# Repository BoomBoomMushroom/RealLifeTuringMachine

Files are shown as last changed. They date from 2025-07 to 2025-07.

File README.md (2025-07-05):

# Real Life Turing Machine
This is a real, physical, and working Turing Machine using an ESP32, off the shelf i2c components, and NFC tags. The Turing machine seems like the lowest level and most basic form of hardware imaginable, so I wanted to try my hand at making one in real life!

# Images
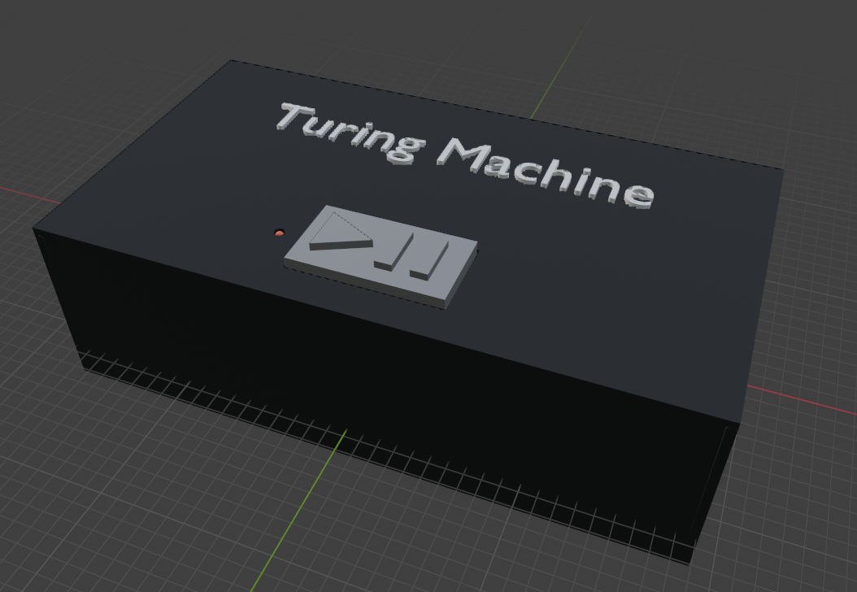
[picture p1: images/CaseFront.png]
Case Front

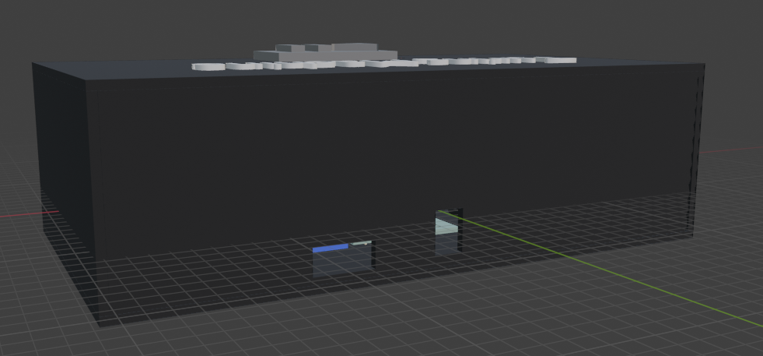
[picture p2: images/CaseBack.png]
Case Back

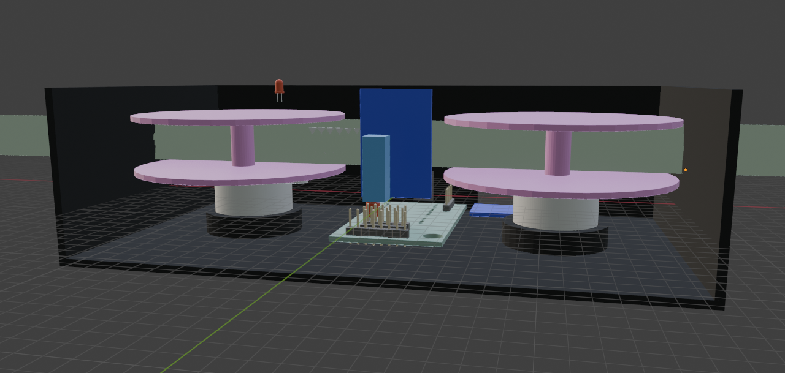
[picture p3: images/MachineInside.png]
Machine Inside

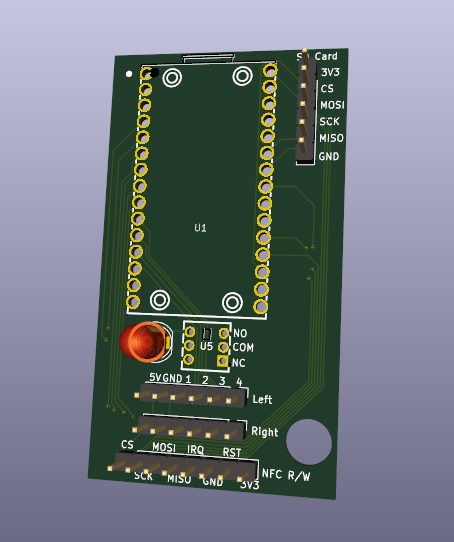
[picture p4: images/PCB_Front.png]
PCB


# Hackatime project name(s)
- RealLifeTuringMachine (8h 31m) TODO: Update this time before submitting
- PCB (2h 23m)
- ESP32_OnlineDevBoard (19m)
- SD_Card_Amazon (10m)
- VHS_Container (4m)
- Blender-VHS_Container (2m)
- Blender-TuringMachineCAD_Models (2m)

# BOM (Check BOM.md for a more in depth bill of materials)
- NFC Stickers
- NFC Reader & Writer Module
- 2x 28BYJ-48 Stepper Motors & Driver boards
- 50ft to 100ft Mylar/Polyester 16mm Film Leader
- ESP32
- SD Card Breakout Board + SD Card (optional)
- Latching Switch 6 Pin
- 3D Printer filament if 3d printing the case
- 3mm LED
- PCB to house all the electronics

TODO: Fill out the checklist and submit

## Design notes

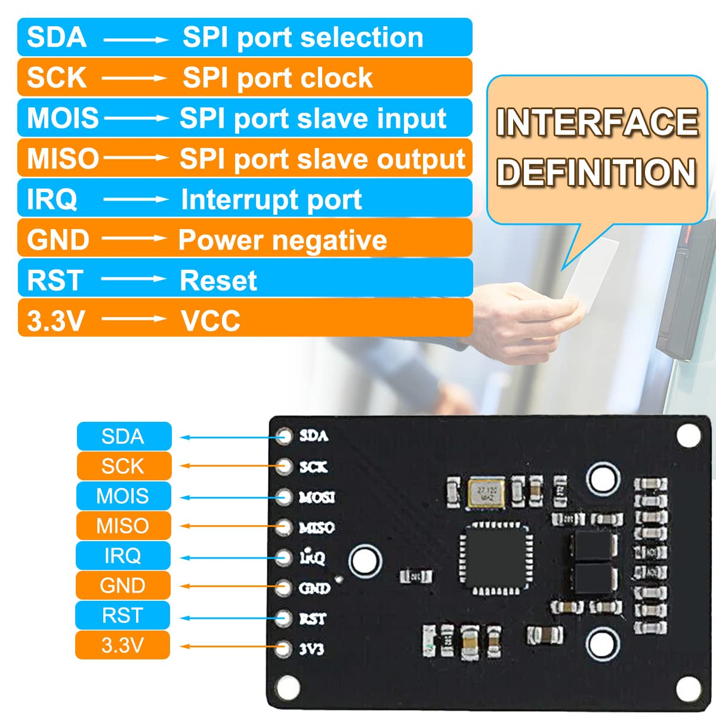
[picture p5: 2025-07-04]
NFC_Reader_Pinout.png

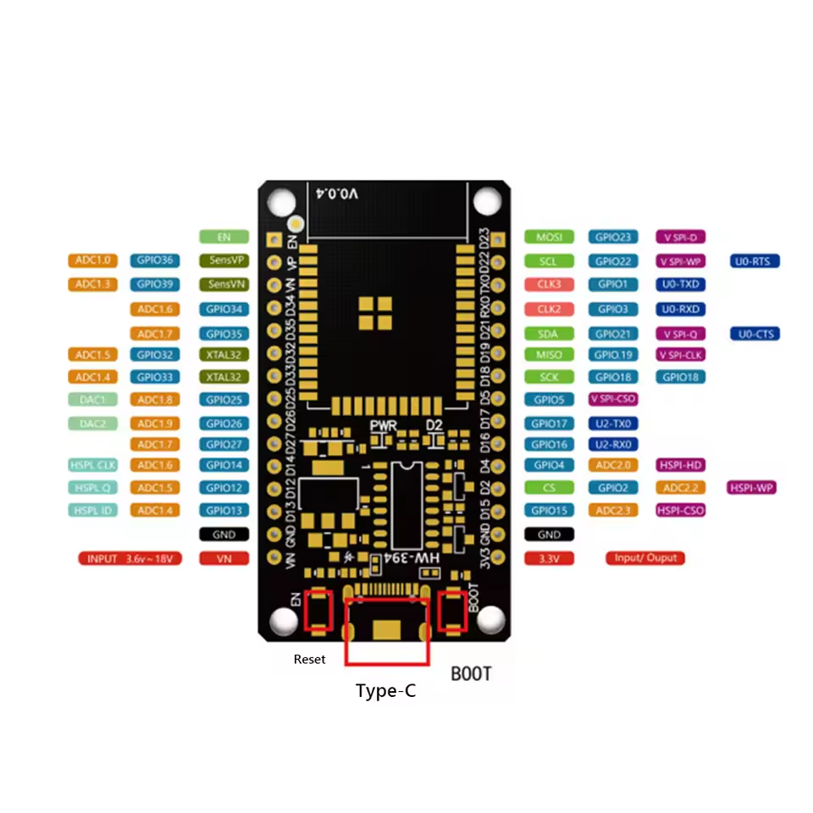
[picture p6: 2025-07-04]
ESP32_Pinout.png

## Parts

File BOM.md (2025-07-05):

# NFC (total: 8.40)
    NFC Stickers: $7.39 100pcs https://www.aliexpress.us/item/3256807427594021.html
    NFC Reader + Writer (i2c?): $1.81 https://www.aliexpress.us/item/2251832854399567.html

# Tape Parts (total: 21.12)
    Stepper Motors + Driver Board: $5.12 total, $2.56 per 28BYJ-48, https://www.aliexpress.us/item/3256806163054731.html
    Tape Material: $16, $8 leader + $8 shipping Mylar/Polyester 16mm Film Leader Cream Single Perf, https://hollywoodfilmsupplies.com/film-supplies/16mm-film-leader-plastic-kodak

# Other Parts (total: 4.67)
    Micro Controller: Aliexpress $1.41 for 2; ESP32, with USB C on it, https://www.waveshare.com/nodemcu-32s.htm  https://www.aliexpress.us/item/3256806150650156.html
    SD Card slot: $1.26 https://www.aliexpress.us/item/3256806636964149.html
    Latching Switch for enable and disabling: $2 https://www.aliexpress.us/item/3256807666498267.html
        Datasheet & Footprints for switch: https://lcsc.com/product-detail/image/KFC7070-Z_C22459508.html

# 3D Printer (optional) (total: 14.99)
    3D Printer Filament PLA: $14.99 https://www.microcenter.com/product/611533/inland-285mm-black-pla-3d-printer-filament-1kg-spool-(22-lbs)

# PCB (total: 5.12)
    PCB from JLCPCB (w/ Global Standard Direct Line Shipping): $5.12

# Grand Total (excluding filament and shipping): $39.31

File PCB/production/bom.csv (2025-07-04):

Designator | Footprint | Quantity | Value | LCSC Part #
D1 | LED_D5.0mm | 1 | EnabledLED
J1 | PinHeader_1x08_P2.54mm_Vertical | 1 | NFC/RFID RW
U1 | ESP32_OnlineDevBoard | 1 | ~
U2, U3, U4 | PinHeader_1x06_P2.54mm_Vertical | 3 | ~
U5 | SW-TH_6P-L7.0-W7.0-P2.00_KFC7070-Z | 1 | ~

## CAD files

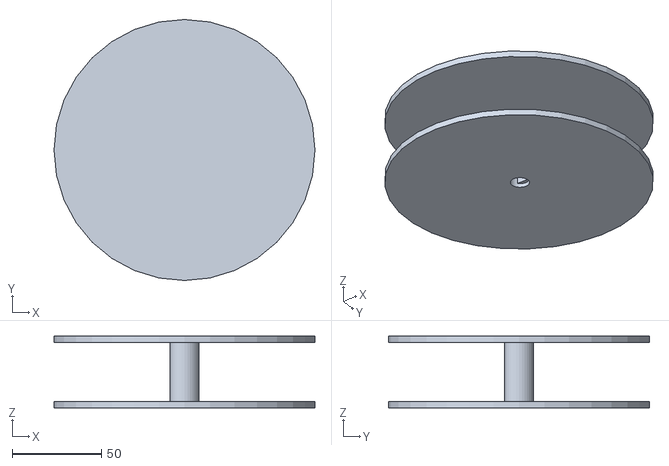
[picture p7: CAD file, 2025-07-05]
CAD_STL/MotorFilmSpool.stl
146.0 x 146.0 x 40.0

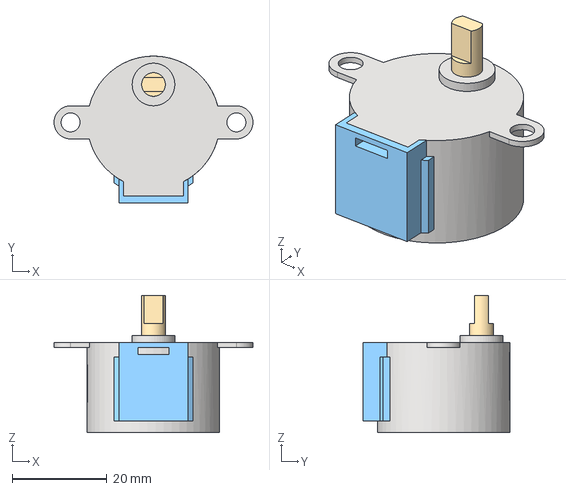
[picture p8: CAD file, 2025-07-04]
TuringMachineCAD_Models/28BYJ-48.step
42.0 x 31.0 x 29.0 mm

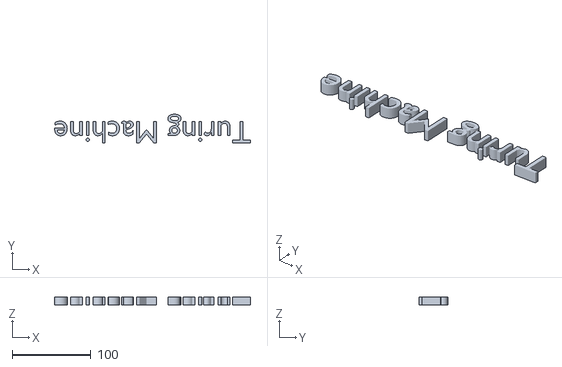
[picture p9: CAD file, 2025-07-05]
CAD_STL/TuringCaseText.stl
248.7 x 36.5 x 10.0

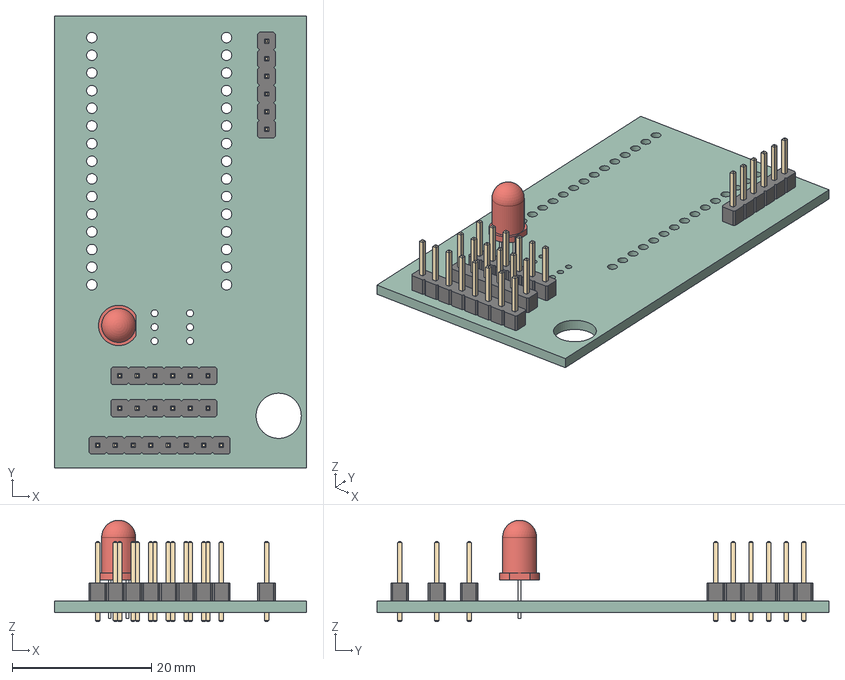
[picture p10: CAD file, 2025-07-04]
TuringMachineCAD_Models/PCB.step
36.2 x 65.0 x 14.6 mm
PinHeader_1x06_P254mm_Vertical x 3
LED_D5.0mm
PinHeader_1x08_P254mm_Vertical
PCB_PCB

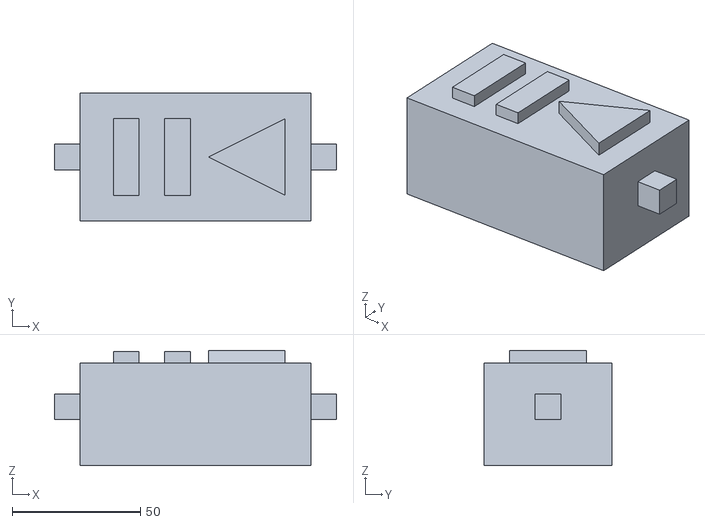
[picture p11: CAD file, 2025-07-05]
CAD_STL/PlayButton.stl
110.0 x 50.0 x 45.0

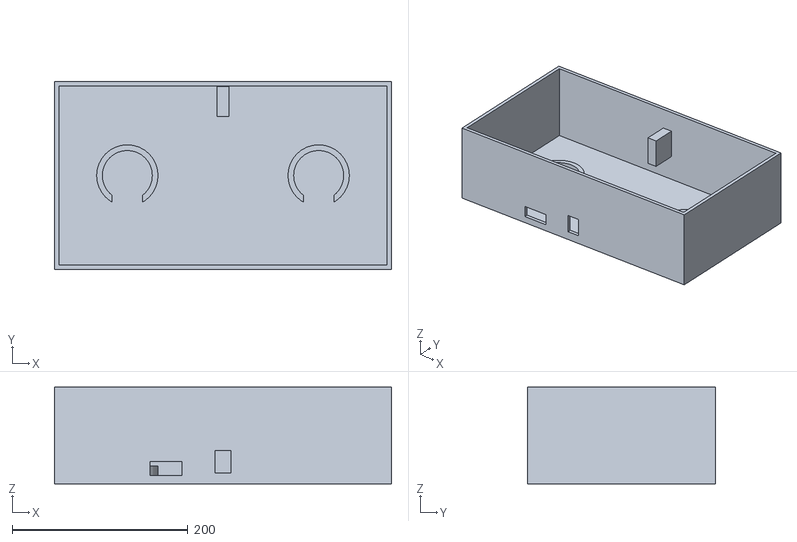
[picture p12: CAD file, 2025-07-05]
CAD_STL/CaseBottomAndWalls.stl
384.0 x 214.0 x 110.0

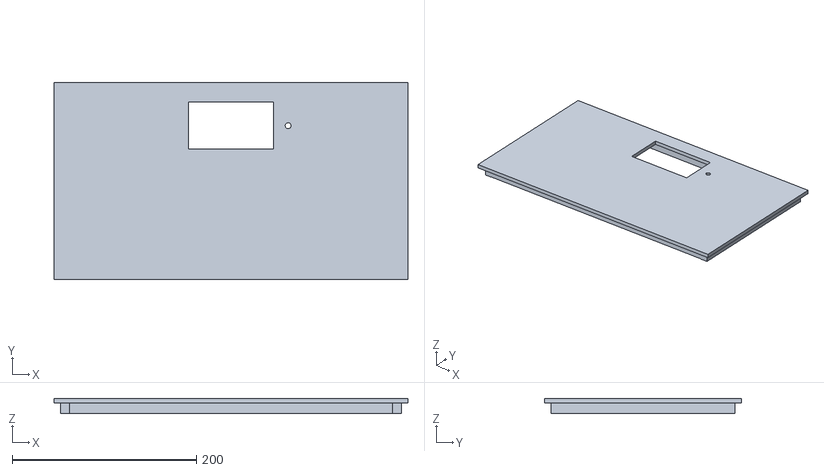
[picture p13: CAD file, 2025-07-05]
CAD_STL/CaseTop.stl
384.0 x 214.0 x 16.5

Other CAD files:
TuringMachineCAD_Models/VHS_Container.blend

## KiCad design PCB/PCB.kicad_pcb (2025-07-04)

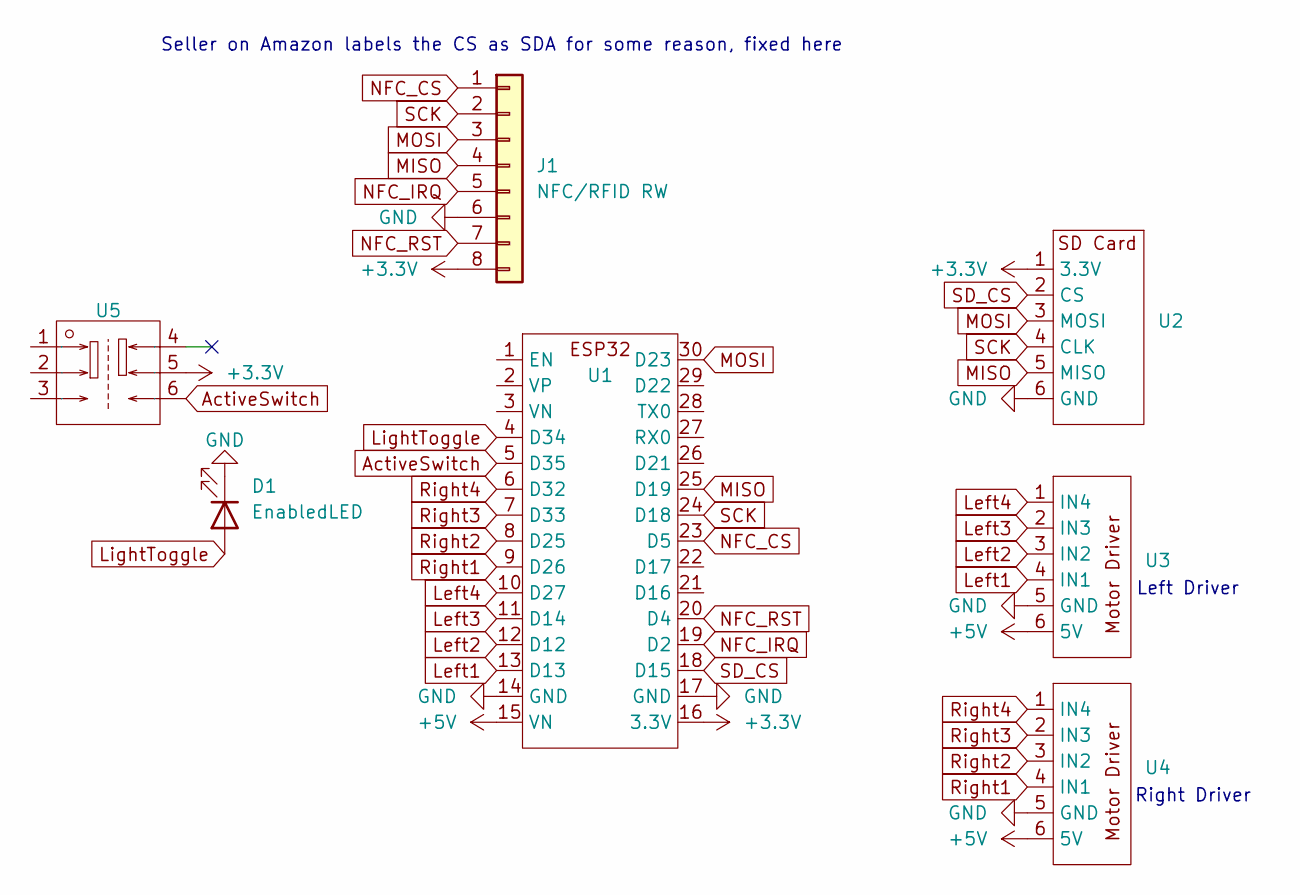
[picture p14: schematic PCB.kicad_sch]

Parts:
D1: EnabledLED; LED_D5.0mm
J1: NFC/RFID RW; PinHeader_1x08_P2.54mm_Vertical
U1: ESP32_OnlineDevBoard
U2, U3, U4: PinHeader_1x06_P2.54mm_Vertical
U5: SW-TH_6P-L7.0-W7.0-P2.00_KFC7070-Z; Manufacturer Part KFC7070-Z; LCSC Part Name KFC7070-Z

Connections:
+3.3V: J1.8, U1.16 (3.3V), U2.1 (3.3V), U5.5
+5V: U1.15 (VN), U3.6 (5V), U4.6 (5V)
ActiveSwitch: U1.5 (D35), U5.6
GND: D1.1 (K), J1.6, U1.14 (GND), U1.17 (GND), U2.6 (GND), U3.5 (GND), U4.5 (GND)
Left1: U1.13 (D13), U3.4 (IN1)
Left2: U1.12 (D12), U3.3 (IN2)
Left3: U1.11 (D14), U3.2 (IN3)
Left4: U1.10 (D27), U3.1 (IN4)
LightToggle: D1.2 (A), U1.4 (D34)
MISO: J1.4, U1.25 (D19), U2.5 (MISO)
MOSI: J1.3, U1.30 (D23), U2.3 (MOSI)
NFC_CS: J1.1, U1.23 (D5)
NFC_IRQ: J1.5, U1.19 (D2)
NFC_RST: J1.7, U1.20 (D4)
Right1: U1.9 (D26), U4.4 (IN1)
Right2: U1.8 (D25), U4.3 (IN2)
Right3: U1.7 (D33), U4.2 (IN3)
Right4: U1.6 (D32), U4.1 (IN4)
SCK: J1.2, U1.24 (D18), U2.4 (CLK)
SD_CS: U1.18 (D15), U2.2 (CS)

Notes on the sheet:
Seller on Amazon labels the CS as SDA for some reason, fixed here
Right Driver
Left Driver

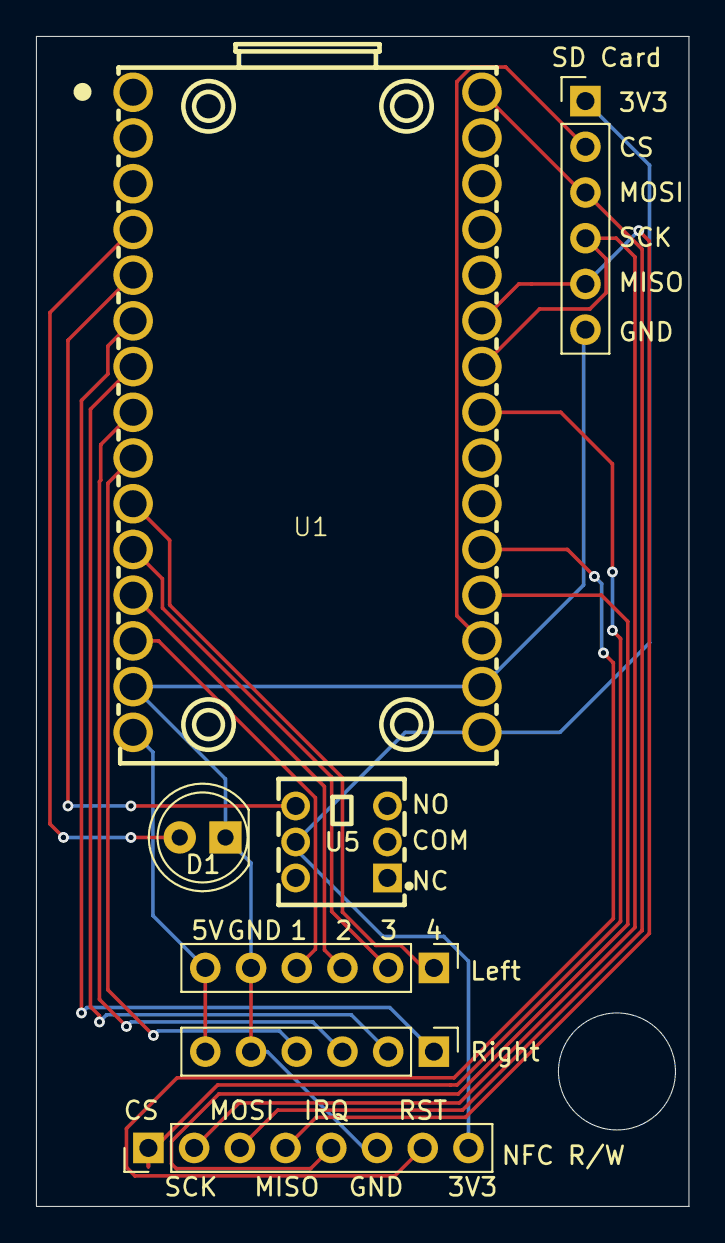
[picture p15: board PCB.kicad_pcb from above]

Board: 2 copper layers, 36.2 x 65.0 mm, 7 parts (0 on the bottom side), 20 nets.

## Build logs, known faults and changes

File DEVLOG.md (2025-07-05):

# Tuesday 7/1/2025
> I was setting up Hackatime for Blender getting ready to make the PCB case. I had the general idea to make it look like a VHS Tape
RealLifeTuringMachine: 12m 55s
VHS_Container: 4m 36s
Blender-VHS_Container: 2m 30s
Blender-TuringMachineCAD_Models: 2m 21s
> 22 minutes spent
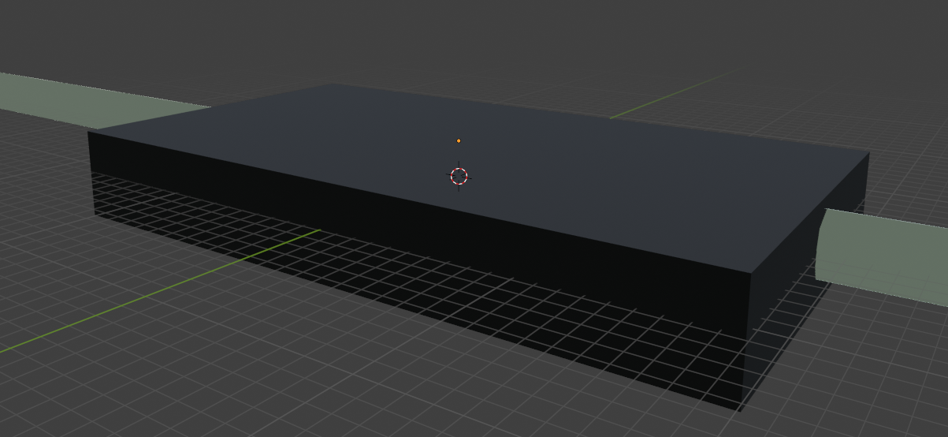
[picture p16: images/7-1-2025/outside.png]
Outside Case

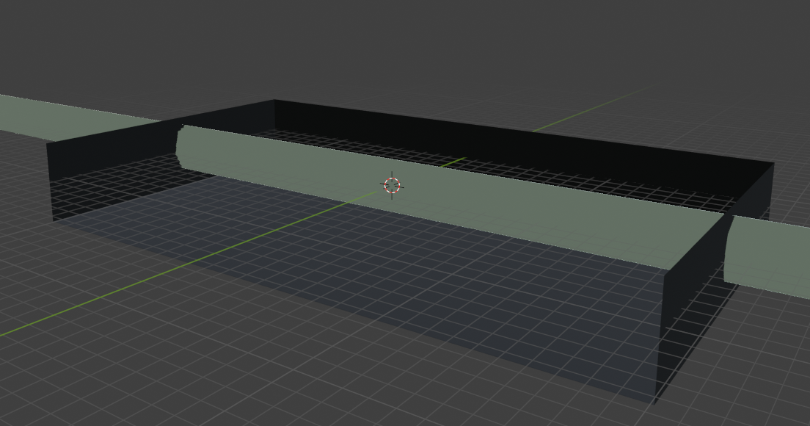
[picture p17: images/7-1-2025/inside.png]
Inside Case


# Wednesday 7/2/2025
> I spent the entire day making the Case for the turing machine. I was looking up parts to use for my build and I found most of them. I found the stepper motors I want to use, imported them into blender and modeled them into the case. I mostly found amazon links to all my parts. I also had to make my case bigger, making it close to twice the width of a real VHS because the tape needs to be on the stepper motor, and the motors are kinda tall.
RealLifeTuringMachine: 2h 12m 55s
> 2 hrs and 12 minutes spent
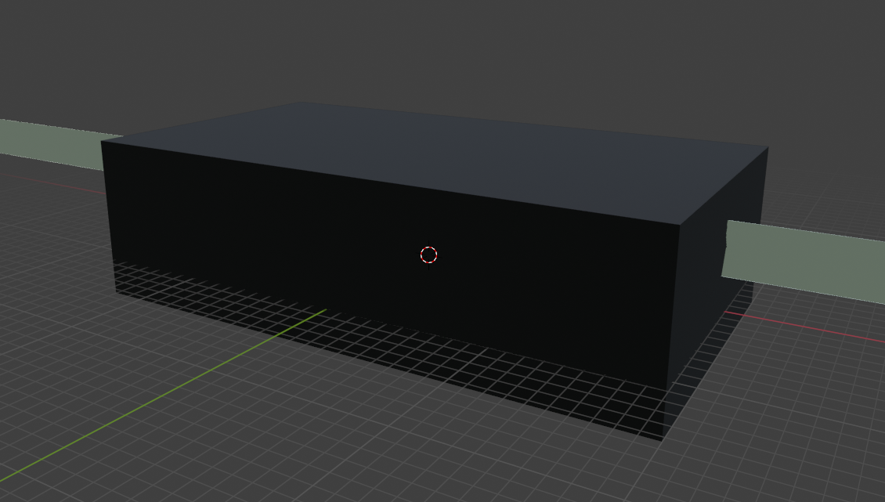
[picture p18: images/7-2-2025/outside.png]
Outside Case

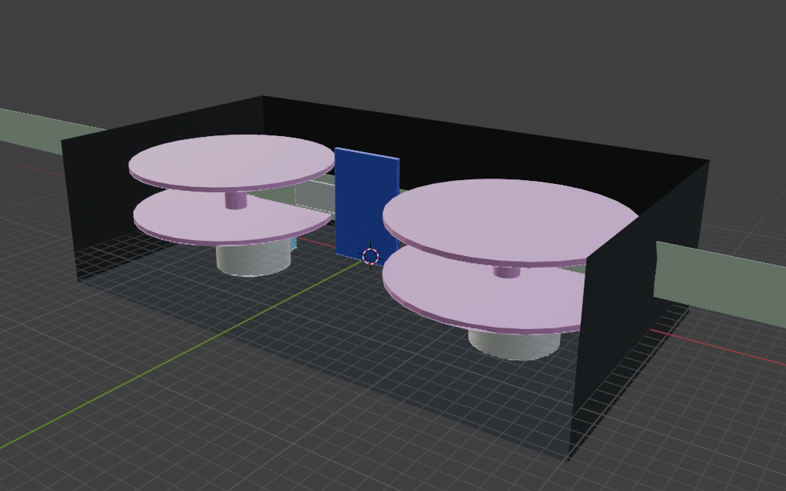
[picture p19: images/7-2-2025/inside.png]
Inside Case


# Thursday 7/3/2025
> I worked on the PCB's schematic after finding all the parts yesterday. I had to find a micocontroller, and an sd card reader. When I found them I made the symbols for them and then added them to the schematic
PCB: 1hr 47m 42s
RealLifeTuringMachine: 55m 9s
ESP32_OnlineDevBoard: 19m 12s
SD_Card_Amazon: 10m 31s
> 3 hrs and 12 minutes spent
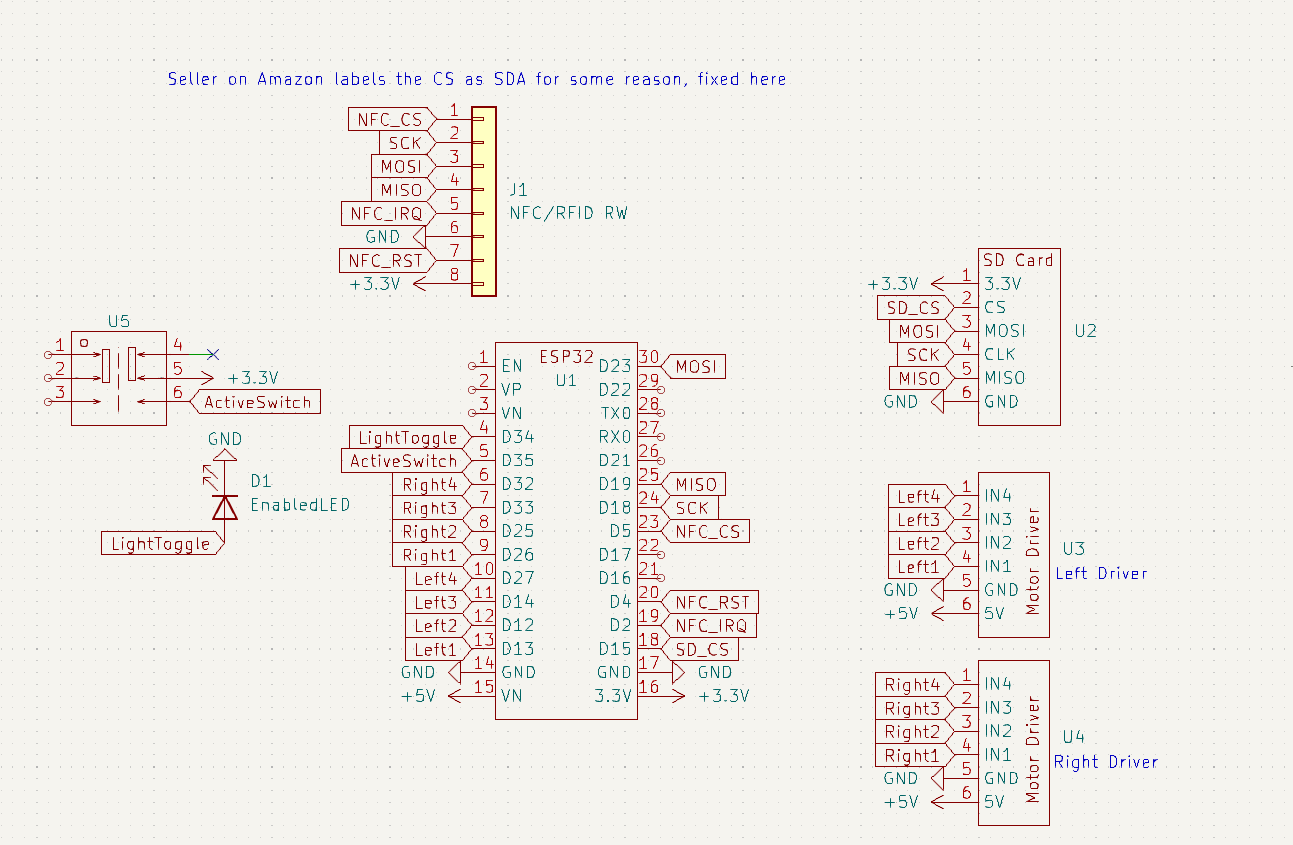
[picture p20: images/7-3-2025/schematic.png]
Schematic


# Friday 7/4/2025
> I finalize the PCB by turning the schematic into a PCB, and got quoted at JLCPCB for 5.12 w/ shipping. I also went through all the BOM links and tried to get them for cheaper. I found many aliexpress parts to use instead of amazon parts. I then wrote the code for the esp32 to have the Turing Machine logic (in Code/TuringMachineCode/TuringMachineCode.ino).
RealLifeTuringMachine: 2h 32m 12s
PCB: 34m 10s
> 3 hrs and 6 minutes spent
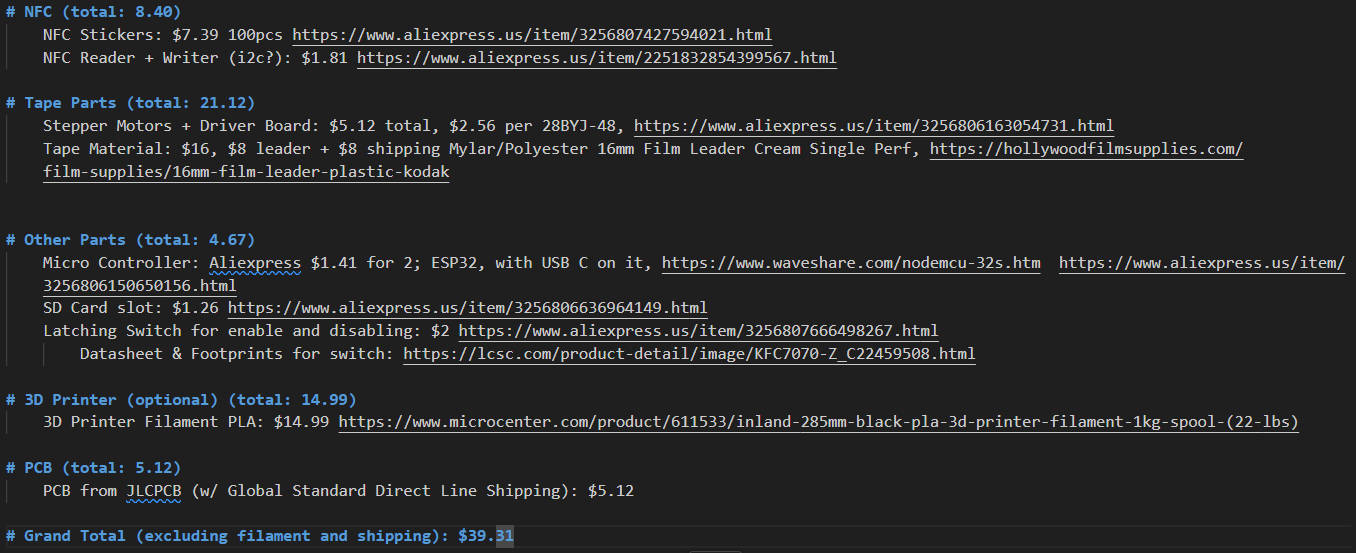
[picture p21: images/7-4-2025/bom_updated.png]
New BOM

PCB

# Saturday 7/5/2025
I finished up the case model by adding supports for some parts like the stepper motor and the latching switch. I also added the button at the top, the LED in the case, holes for the SD card & USB C, and the text at the. I also exported all the things from blender to stls for 3d printing.
RealLifeTuringMachine: 2h 12m 51s
> 2hrs and 31 minutes spent
Case
Inside Case

# Total time spend:
11h 2m (according to hackatime)

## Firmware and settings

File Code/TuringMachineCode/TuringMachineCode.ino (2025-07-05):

#include <Arduino.h>
#include <vector>

// Pins
#define LightPin 34
#define ActiveSwitchPin 35
#define NFC_IRQ_Pin 2
#define NFC_RST_Pin 4
// Motors
#define RightMotorPin4 32
#define RightMotorPin3 33
#define RightMotorPin2 25
#define RightMotorPin1 26
#define LeftMotorPin4 27
#define LeftMotorPin3 14
#define LeftMotorPin2 12
#define LeftMotorPin1 13
int RightMotorPins[] = {RightMotorPin1, RightMotorPin2, RightMotorPin3, RightMotorPin4};
int LeftMotorPins[] = {LeftMotorPin1, LeftMotorPin2, LeftMotorPin3, LeftMotorPin4};
// SPI
#include <SPI.h>
#define MOSI 23
#define MISO 19
#define SCK 18
#define NFC_CS 5
#define SD_CS 15
SPIClass spiBus(VSPI);

// SD Card
#include <SD.h>
#define DATA_FILE_NAME "program.json" // placeholder name, figure out a name and extention later

// NFC
#include <MFRC522.h>
MFRC522 mfrc522(NFC_CS, NFC_RST_Pin); // Create MFRC522 instance.
MFRC522::MIFARE_Key key;

// Turing Machine
// Using my virtual turing machine for working code (https://github.com/BoomBoomMushroom/TuringMachineWebsite/blob/main/index.html)
#define HALT_STATE_ID -1
#define ACCEPT_STATE_ID -2
#define REJECT_STATE_ID -3
#define LEFT_MOVE false
#define RIGHT_MOVE true
struct state {
  int id; // note multiple states can have the same id; it is used for the different read values
  uint8_t readValue;
  uint8_t writeValue;
  bool moveDirection; // false for left, right for true
  int nextId; // you can use the HALT, ACCEPT, or REJECT state ids here
}
std::vector<state> states;
int currentStateID = 0; // I need to figure out some way to allow for virtually infinite state IDs, since rn we're limited by the int limit, and it's harder to read than a string

void setup() {
  // put your setup code here, to run once:
  Serial.begin(9600);
  while (!Serial) {
    ; // wait for serial port to connect. Needed for native USB port only
  }
  pinInit();
  
  spiBus.begin(SCK, MISO, MOSI, NFC_CS);
  mfrc522.PCD_Init();
  mfrc522.PCD_Init(&spiBus, NFC_CS);

  // Init SD card
  initSDCard();
  // TODO: When I get the machine built I will then setup the SD Card reading and loading code.

  // load the 3 state 2 symbol busy beaver program as an example
  states.clear();
  states.push_back({ 0, 0, 1, RIGHT_MOVE, 1 });
  states.push_back({ 0, 1, 1, RIGHT_MOVE, HALT_STATE_ID });

  states.push_back({ 1, 0, 0, RIGHT_MOVE, 2 });
  states.push_back({ 1, 1, 1, RIGHT_MOVE, 1 });

  states.push_back({ 2, 0, 1, LEFT_MOVE, 2 });
  states.push_back({ 2, 1, 1, LEFT_MOVE, 1 });
}

void loop() {
  // put your main code here, to run repeatedly:
  // NFC_loop();

  bool isActive = digitalRead(ActiveSwitchPin) == HIGH;
  if(isActive == false){
    // The button isn't pressed down, so the machine is inactive
    setLEDStatus(false);
    return;
  }

  if(currentStateID == HALT_STATE_ID || currentStateID == ACCEPT_STATE_ID || currentStateID == REJECT_STATE_ID){
    // blinking codes: 1 blink for halt, 2 blinks for accept, and 3 blanks for reject
    int numberOfBlinks = 1; // default case for HALT
    if(currentStateID == ACCEPT_STATE_ID){ numberOfBlinks = 2; }
    if(currentStateID == REJECT_STATE_ID){ numberOfBlinks = 3; }
    blinkLED(numberOfBlinks, 150); // 150ms between each blink
    delay(1500); // wait 1.5 seconds between each blink set
    return; // Don't allow the machine to tick when in one of these states because it is the end of the program.
  }

  setLEDStatus(true);
  TuringMachineStep();
  delay(100); // wait 100ms before doing the next step
}

bool TuringMachineStep(){
  uint8_t nfc_block = 2

  uint8_t readBuffer[18];
  bool readSuccess = NFC_ReadTag(nfc_block, readBuffer); // Read sector 2 in to the read buffer
  if(readSuccess == false){ return false; } // TODO: Figure out why it failed

  uint8_t valueAtHead = readBuffer[0]; // For now we will only use 1 byte of the tag to store a symbol. TODO: Expand this to allow multi byte symbols, and maybe multi block symbols
  state specificStateRule = NULL;
  for(int i=0; i<states.size(); i++){
    state compareState = states[i];
    if(compareState.id != currentStateID){ continue; }
    if(compareState.readValue != valueAtHead){ continue; }
    specificStateRule = compareState;
    break; // we found out state so we should exit the loop;
  }
  if(specificStateRule == NULL){ return false; }

  // maybe to save resources we can write over the read buffer?
  uint8_t writeBuffer[16]; // we cannot write the last 2 bytes like the read because those are checksums.
  memset(writeBuffer, 0, 16); // zero out the buffer before putting data into it
  writeBuffer[0] = specificStateRule.writeValue;

  bool writeSuccess = NFC_WriteTag(nfc_block, writeBuffer);
  if(writeSuccess == false){ return false; } // TODO: Figure out why it failed

  moveTape(specificStateRule.moveDirection == RIGHT_MOVE);
  currentStateID = specificStateRule.nextId; // Set the next state id

  return true;
}

void moveTape(bool isRight){
  // TODO: When I get the machine built I need to find how much I actually need to move the motors to get to a new tag. But for now I will use 512 (one full rotation)
  // Maybe we can just keep moving until we hit another tag?
  // Also I am currently assuming clockwise if moving right but double check this when I get the machine
  int amountOfStepsToMove = 512; // 1 full step. this is temporary until I get the physical machine
  stepMotors(amountOfStepsToMove, isRight); // Right is clockwise so just use that bool
}

void NFC_loop(){
  // Look for new cards
  if (!mfrc522.PICC_IsNewCardPresent() || !mfrc522.PICC_ReadCardSerial()) {
    return;
  }

  uint8_t buffer[18];
  if (NFC_ReadTag(4, buffer)) {
    Serial.println("Read 18 bytes (data + CRC):");
    for (int i = 0; i < 18; i++) {
      Serial.printf("%02X ", buffer[i]);
    }
    Serial.println();
  } else {
    Serial.println("Failed to read NFC tag.");
  }

  mfrc522.PICC_HaltA();
  mfrc522.PCD_StopCrypto1();
  delay(2000);
}

bool NFC_WriteTag(uint8_t block, uint8_t dataBlock[16]) {
  //uint8_t block = 4; // Block to write (not sector 0!)

  // Authenticate
  MFRC522::StatusCode status = mfrc522.PCD_Authenticate(
    MFRC522::PICC_CMD_MF_AUTH_KEY_A, block,
    &mfrc522.MIFARE_Key(), &mfrc522.uid
  );

  if (status != MFRC522::STATUS_OK) {
    Serial.print("Auth failed: ");
    Serial.println(mfrc522.GetStatusCodeName(status));
    return false;
  }

  // Write data
  status = mfrc522.MIFARE_Write(block, dataBlock, 16);
  if (status != MFRC522::STATUS_OK) {
    Serial.print("Write failed: ");
    Serial.println(mfrc522.GetStatusCodeName(status));
    return false;
  }

  Serial.println("Write successful.");
  return true;
}

bool NFC_ReadTag(uint8_t block, uint8_t* outputBuffer) {
  //uint8_t block = 4;
  uint8_t buffer[18];
  uint8_t size = sizeof(buffer);

  // Authenticate
  MFRC522::StatusCode status = mfrc522.PCD_Authenticate(
    MFRC522::PICC_CMD_MF_AUTH_KEY_A, block,
    &mfrc522.MIFARE_Key(), &mfrc522.uid
  );

  if (status != MFRC522::STATUS_OK) {
    Serial.print("Auth failed: ");
    Serial.println(mfrc522.GetStatusCodeName(status));
    return false;
  }

  // Read data
  status = mfrc522.MIFARE_Read(block, buffer, &size);
  if (status != MFRC522::STATUS_OK) {
    Serial.print("Read failed: ");
    Serial.println(mfrc522.GetStatusCodeName(status));
    return false;
  }

  // Copy the data to the output buffer
  memcpy(outputBuffer, buffer, 18);
  return true;
}

// "interrupt service routine" Idk when this is triggered. Maybe when the chip detects a card and then we read it from here.
void NFC_ISR(){}

void setLEDStatus(bool isOn){
  digitalWrite(LightPin, isOn ? HIGH : LOW);
}

void blinkLED(int numberOfTimes, int blinkSpacing,){
  while(numberOfTimes > 0){
    setLEDStatus(true);
    delay(blinkSpacing);
    setLEDStatus(false);
    delay(blinkSpacing);
    numberOfTimes--;
  }
}

void stepMotors(int steps, bool isClockwise){
  // 512 steps is 1 full rotation
  // TODO: Actually determine what is clockwise and what is not
  while(steps--){
    for(int i=0;i<4;i++)
    {
      int index = i;
      if(isClockwise==false){
        index -= 3; // subtract the highest index (which is 3, 4 is not exclusive because we index at 0)
        index = abs(index);
        // This should flip the index when we go the other way
        // 0 - 3 = -3 (3)
        // 1 - 3 = -2 (2)
        // 2 - 3 = -1 (1)
        // 3 - 3 = 0 (0)
      }
      digitalWrite(RightMotorPins[index],1);
      digitalWrite(LeftMotorPins[index],1);
      delay(10);
      digitalWrite(RightMotorPins[index],0);
      digitalWrite(LeftMotorPins[index],0);
    }
  }
}

void initSDCard(){
  Serial.print("Initializing SD card...");

  if (!SD.begin(chipSelect, spiBus)) {
    Serial.println("initialization failed. Things to check:");
    Serial.println("1. is a card inserted?");
    Serial.println("2. is your wiring correct?");
    Serial.println("3. did you change the chipSelect pin to match your shield or module?");
    Serial.println("Note: press reset or reopen this serial monitor after fixing your issue!");

    //while (true);
    return; // Don't hang the program, let's just return
  }

  Serial.println("initialization done.");

  // open the file. note that only one file can be open at a time,
  // so you have to close this one before opening another.
  File dataFile = SD.open(DATA_FILE_NAME);

  // if the file is available, write to it:
  if (dataFile) {

    while (dataFile.available()) {

      Serial.write(dataFile.read());
      // TODO: Load the turing machine data and states

    }

    dataFile.close();

  }
  else { // if the file isn't open, pop up an error:
    Serial.println("error opening datalog.txt");
  }
}

void pinInit()
{
  pinMode(LightPin, OUTPUT);
  pinMode(NFC_RST_Pin, OUTPUT);
  pinMode(NFC_CS, OUTPUT);
  pinMode(SD_CS, OUTPUT);
  pinMode(RightMotorPin4, OUTPUT);
  pinMode(RightMotorPin3, OUTPUT);
  pinMode(RightMotorPin2, OUTPUT);
  pinMode(RightMotorPin1, OUTPUT);
  pinMode(LeftMotorPin4, OUTPUT);
  pinMode(LeftMotorPin3, OUTPUT);
  pinMode(LeftMotorPin2, OUTPUT);
  pinMode(LeftMotorPin1, OUTPUT);

  pinMode(ActiveSwitchPin, INPUT_PULLDOWN);

  // idk if the interrupt is necessary so i'll comment it out for now
  //attachInterrupt(digitalPinToInterrupt(NFC_IRQ_Pin), NFC_ISR, CHANGE); // idk when the interupt should be triggered so I put CHANGE, but LOW, RISING, and FALLING all are options.
}

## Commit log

2025-07-04 Finished PCB and working on CAD
    [28BYJ-48.step, PCB.kicad_pcb, PCB.kicad_sch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]
2025-07-05 Finished and ready to submit
    [CaseBottomAndWalls.stl, CaseTop.stl, MotorFilmSpool.stl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]
